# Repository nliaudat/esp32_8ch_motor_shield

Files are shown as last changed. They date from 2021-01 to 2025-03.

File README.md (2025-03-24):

# An ESP32 8 channels motor controller (shield) | Floor heating controller for proportional actuator
(Can replace Homematic IP Floor Heating Actuator [HmIP-FALMOT-C12] ~210$ + [CCU3] ~150$)



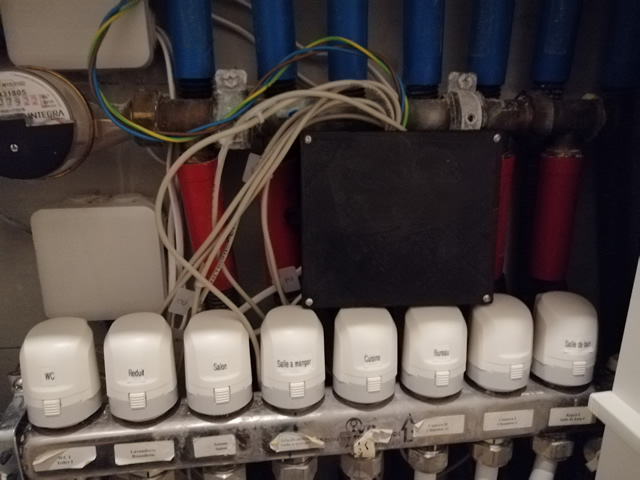
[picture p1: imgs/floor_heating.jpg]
floor_heating


The ready to go board costs less than 15$ (excluding shipping)

## Project rules : 
This project have rules : open hardware and sources, but not open-bar :)
* https://github.com/nliaudat/esp32_8ch_motor_shield/wiki/Project-rules

## 2 Goals : 

* Make a floor heating controller for proportionnal valves ([look at advantages of proportionnal valves](https://github.com/nliaudat/esp32_8ch_motor_shield/wiki/Advantages-of-proportionnal-valves-instead-of-on-off-valves) )
* ESP motor shield (done in v58 rev 1.49 )
    
## Functionalities : 
* Can control 8 DC motors or 4 steppers motor
* Can drive 8 Homematic valve actuators [HmIP-VDMOT] (~15$ each)
* The card use a ESP32-WROOM-32D as logics and wifi connection. (You can get a 32U if you want an external antenna).
* It now supports the ESP32-C3 supermini
* The software runs under esphome to be easy to customize and linked with https://www.home-assistant.io 
* Can be extended up to 16 channels (I recommend to get 2 boards for better performances, but the shifts registers can be extended up to 4 [shiftregOut](https://github.com/nliaudat/esp32_8ch_motor_shield/blob/main/shiftregOut.md))
* Use BEMF (back electromotive force) from motors to get endstops
* Can be directly linked to external temperature sensors (wifi,BLE, or via available [free pins](https://github.com/nliaudat/esp32_8ch_motor_shield/blob/main/extension.md))
* 2 onewire connectors (to have precise IN/OUT temperature control over heating circuit)
* USB-C power input or 5-12V input
* Easily [hackable](https://github.com/nliaudat/esp32_8ch_motor_shield/blob/main/hack.md)

## Fabrication : 

* PCB can be ordered with chips assembled at JLPCB for 13$/unit. (:warning: For old AC version, you have to isolate the AC part with tape)
* The new version use DC input only with usb-c up to 3A (or custom 5-12V input)
* ESP32-WROOM-32D devkit with 38 pin costs approx 3.8$ . The ESP32-C3 supermini approx 2.5$
* Box is 3D printed

## Firmware : 
* Floor heating : https://github.com/nliaudat/floor-heating-controller
* Motor control : https://github.com/nliaudat/esphome-8-ch-motor-controller

## The futur is : Diy proportionnal valves | smart proportional actuator (TRV) with Esp-C3 mcu
https://github.com/nliaudat/floor-heating-proportional-valve | need help !

## Produce your PCB Controller and Enclosure

We tried to ease the steps to get you going to produce the Enclosure and order/assemble your Controller-Board. Please have a look at 
the [`HOWTO get going`](./HOWTO_get_going_as_floor_heating_controller.md) documentation.

## PCB sharing
[https://oshwlab.com/nliaudat/floor_heatin_controller_v61](https://pro.easyeda.com/editor#id=15bc77acaa4147fca2a36e92e8cc8681)

## Licence: 
* Creative Commons Attribution-NonCommercial-ShareAlike 4.0 International (CC-BY-NC-SA)
* No commercial use

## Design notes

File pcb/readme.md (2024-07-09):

# Design printouts

All schematics and pcb are in https://github.com/nliaudat/esp32_8ch_motor_shield/releases

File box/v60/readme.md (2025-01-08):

Many thank @MrAges

https://github.com/nliaudat/esp32_8ch_motor_shield/discussions/70#discussioncomment-11770972

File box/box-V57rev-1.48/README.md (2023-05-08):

# Enclosure for version V57 rev 1.48
This enclosure is divided into two parts: the bottom and the top.

## Bottom enclosure
The bottom enclosure, named "bottomCase3dModel", is designed to accommodate a PCB and has 3 mounting holes (M3x8mm) to secure the PCB. Additionally, it has 4 holes to attach the enclosure to a wall. On the right side, there is an opening for a PG 9 4-8mm cable gland (PGS9) used for power cable mounting. At the front of the enclosure, there are 8 holes for RJ11 jacks.

## Top enclosure
The top enclosure comes in two versions:

"topCase3dModelwithWagoAndAntenna" includes additional WAGO holders and an opening for an SMA antenna jack. WAGO connectors are used to connect DS18B20 thermometers.

"topCase3dModel" is a plain version with no additional holes or mounting options.

The enclosure is 40mm high (52mm for the version with WAGO holders), 100mm wide, and 155mm long.

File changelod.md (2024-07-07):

## New version 1.3 : 
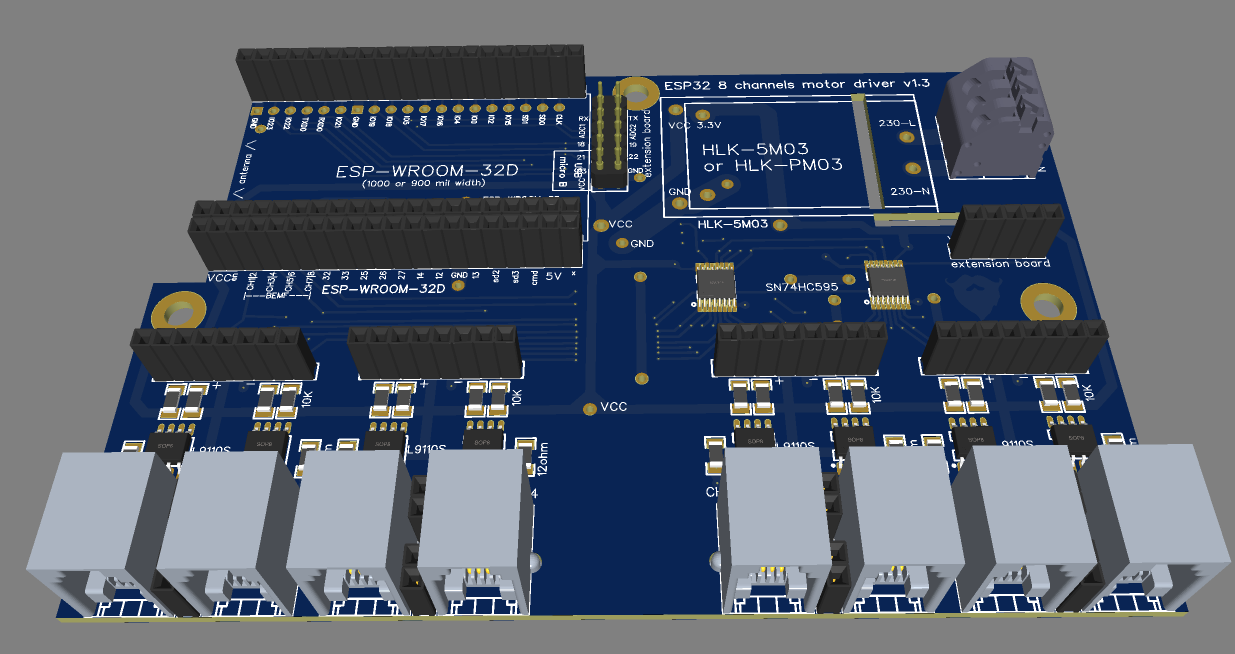
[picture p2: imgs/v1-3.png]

* Compatible with HKL-5M03 or HKL-PM03, or with 5V version (HKL-5M05 or HKL-PM05)
* Compatible with 1000 or 900 mil ESP32 board width

## New version 1.4 : 
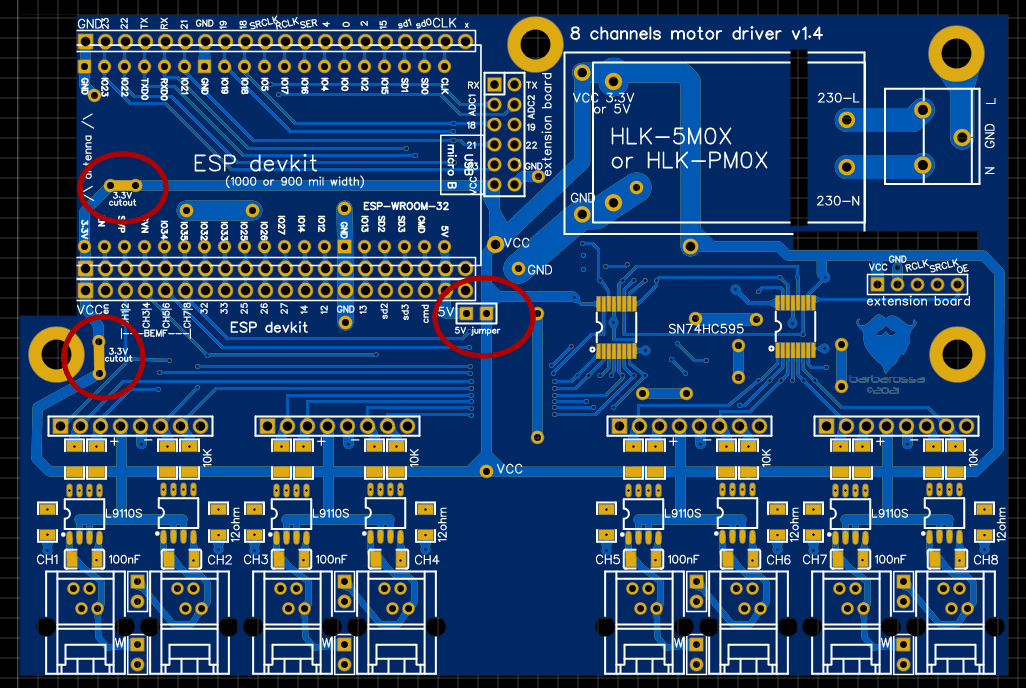
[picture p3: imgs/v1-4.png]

* Input power can be 5V to 12V
* 5V Jumper + 3.3V exposed copper cutout

## New version v53 rev 1.19 : 
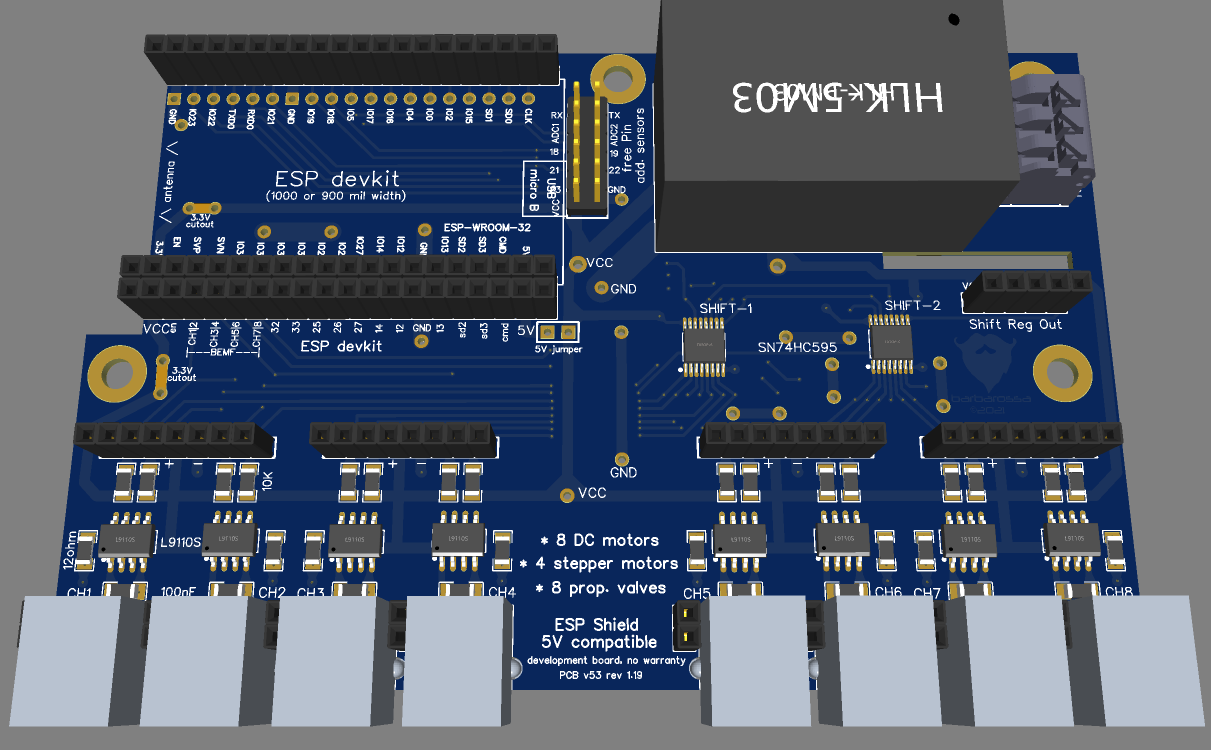
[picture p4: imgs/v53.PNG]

* Complete rebuild
* All part can be assembled at JLPCB
* Costs rise to 25$ / board (ESP not included, shipping included)
* Fix issue [#5] (https://github.com/nliaudat/esp32_8ch_motor_shield/issues/5)
* Fix HLK-PM03 footprint
* Change L9110s chips (the old one was not available anymore)
* change version number to real job

## New version v54 rev 1.34 : 
* Change 230V input socket with screw
* Fix regression in HLK-PM03 footprint
* Change resistors to 1.07 ohm

## New version with DC input power (4.9-18 V 5A - usb and DC 2.5/6.3 plug): 


## New version v54 rev 1.39 : 
* fix CH6 input shorted to CH7/8 BEMF [#27](https://github.com/nliaudat/esp32_8ch_motor_shield/issues/27)

## New version v55 rev 1.45 : 
* Add operational amplifier to ADC inputs

* Easyeda project getting [public](https://easyeda.com/editor#id=240c2bd91cde438f93348d56e1ae4e72|420e6f6085d643fc9c5df7bfbe9595bf|f15c181c211e4aebaf86420464abe718|b3e9b48180db4901b45d0292a792846e|60a1b0936f664eb8b9e5f7402068a21b|7744c3e75c54448eb9fed788f130dd96|78ed6c97623e4c1f929c753245e2f96b)

## New version v57 rev 1.48 : 
* Replace the 1.07R with 2 ohms
* Custom resistors for BEMF (exposed layer to cut out)
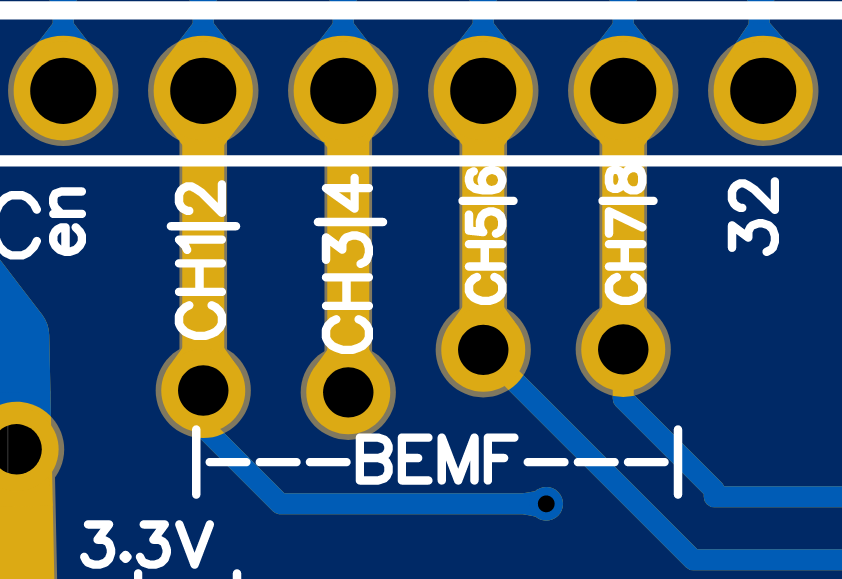
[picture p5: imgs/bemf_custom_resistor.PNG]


## New version v58 rev 1.49 : 
* Replace the RJ11 with screw terminals ( the RJ11 was too specific for "HmIP-VDMOT") (look at [VdMot wiring](https://github.com/nliaudat/esp32_8ch_motor_shield/blob/main/VDMOT_wiring.md))
* Make the board compatible with all kind of motors (2.5 to 6V)
* The easyeda sources are not available anymore (more than 50 developpers has anounced and nobody make a public commit since 3 years)
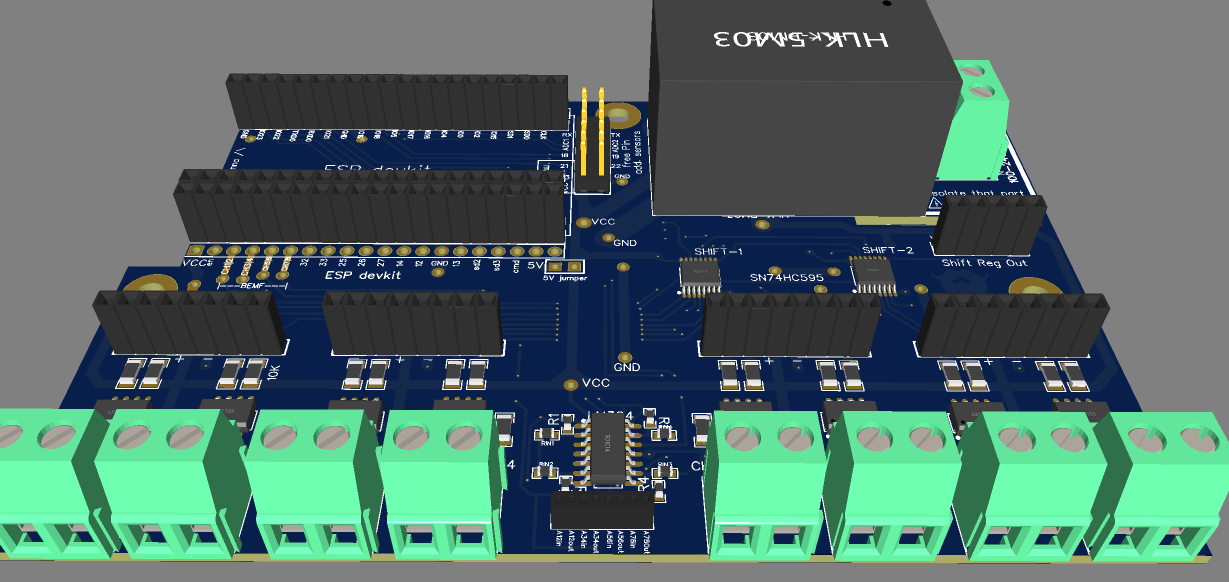
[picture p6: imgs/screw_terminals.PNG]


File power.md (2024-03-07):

# The shield itself:
* accept a wide supply voltage range from 3.3V to 12V
* 800mA continuous current output capability per channel
* peak current capability up to 2.0A

# AC Power for ESP : 
3.3v power can be HKL-5M03 or HKL-PM03 or anything else

# DC Power : 
Any DC-DC Buck Converter Step Down Module

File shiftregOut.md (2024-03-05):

To link a 2nd board (without esp32) , you can use the shift reg out pins : 



linked to the other pcb (without esp32)



QH' output must be linked to SER input

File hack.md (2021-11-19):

# Hackable
* Every board Pin has its own second weldable slot
* Can work with 5V controller board like Arduino series

## Samples :
#### Replacing BEMF resistors
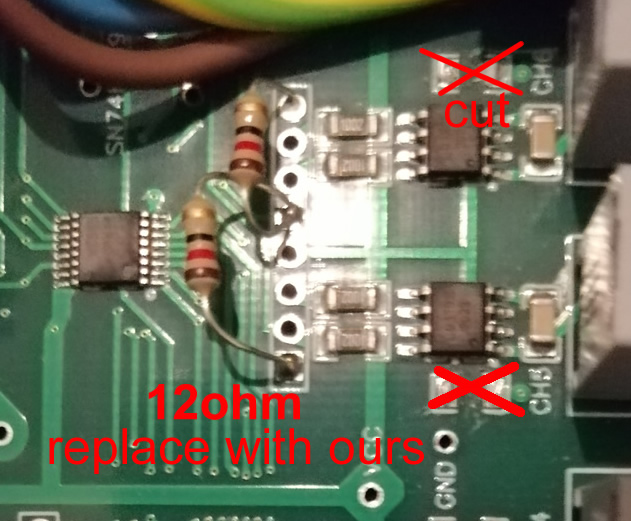
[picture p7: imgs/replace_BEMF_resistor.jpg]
replace BEMF resistor


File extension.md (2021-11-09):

They are 7 free pin available to add custom sensors

Capture

Capture2

Look at [schematics.pdf](https://github.com/nliaudat/esp32_8ch_motor_shield/blob/main/PCB/Schematic.pdf) for details.

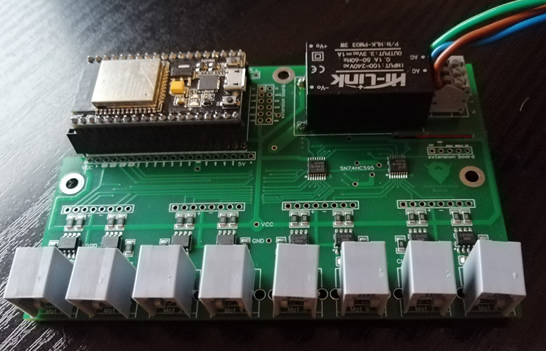
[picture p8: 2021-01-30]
imgs/board.jpg

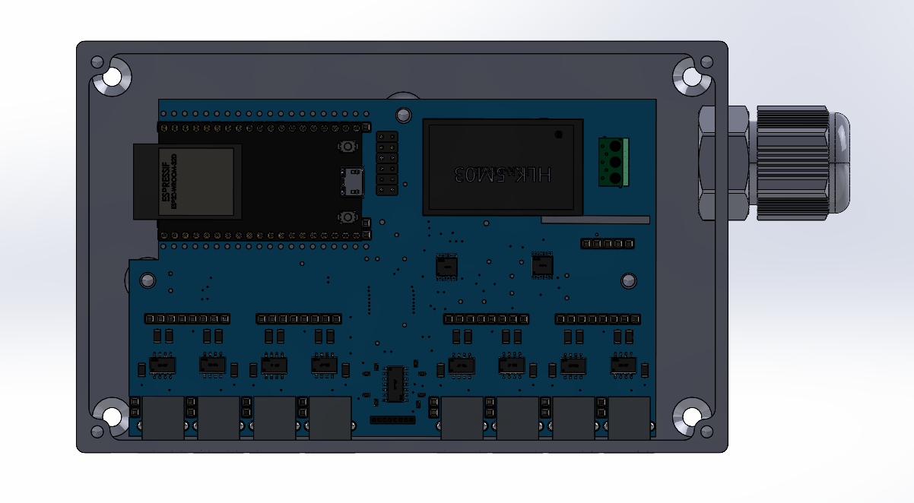
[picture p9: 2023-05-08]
box/box-V57rev-1.48/img/bottomCase3dModel - model2.png

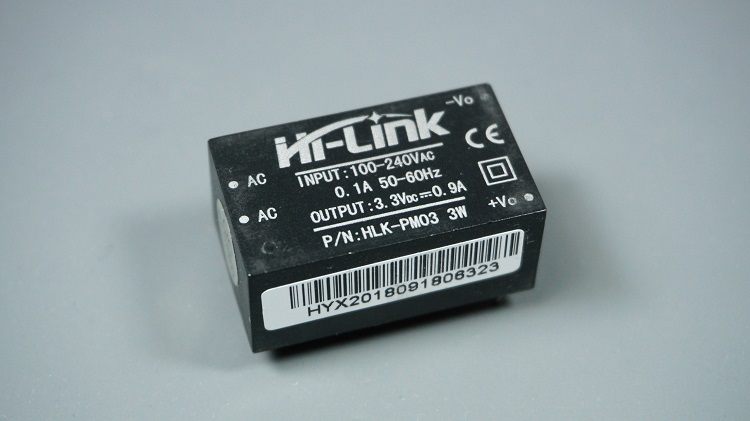
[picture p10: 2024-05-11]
imgs/HLK-PM03.jpg

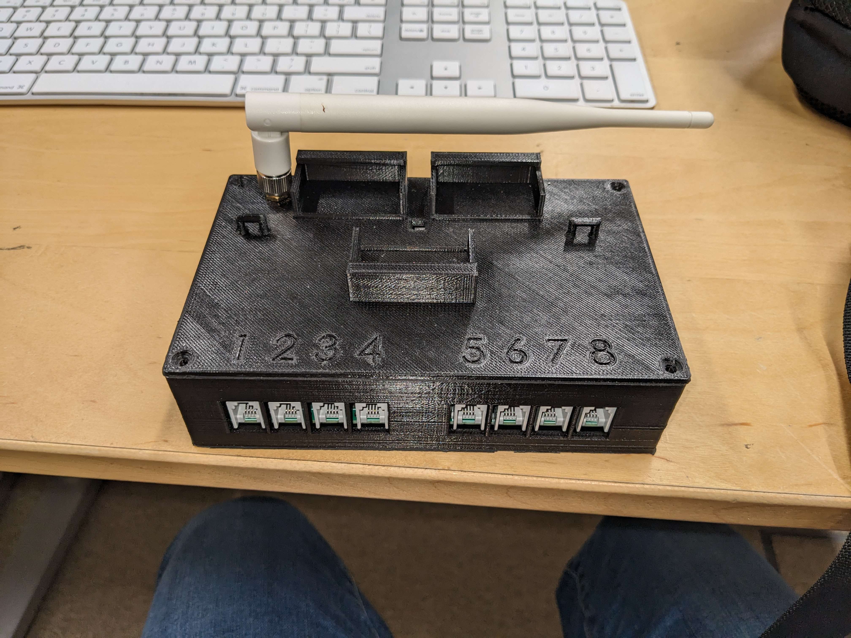
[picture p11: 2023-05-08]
box/box-V57rev-1.48/img/topCase3dModelwithWagoAndAntenna - real photo 2.jpg

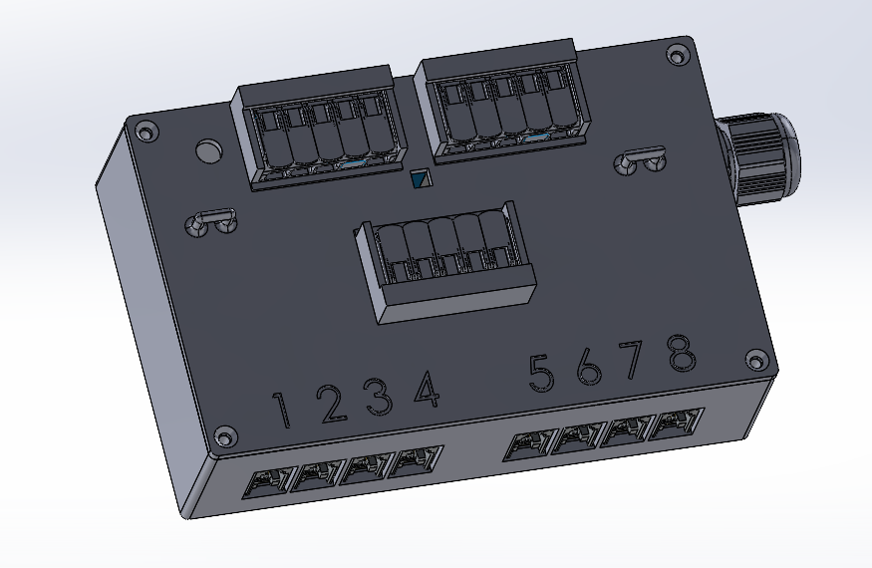
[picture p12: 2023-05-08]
box/box-V57rev-1.48/img/topCase3dModelwithWagoAndAntenna - model.png

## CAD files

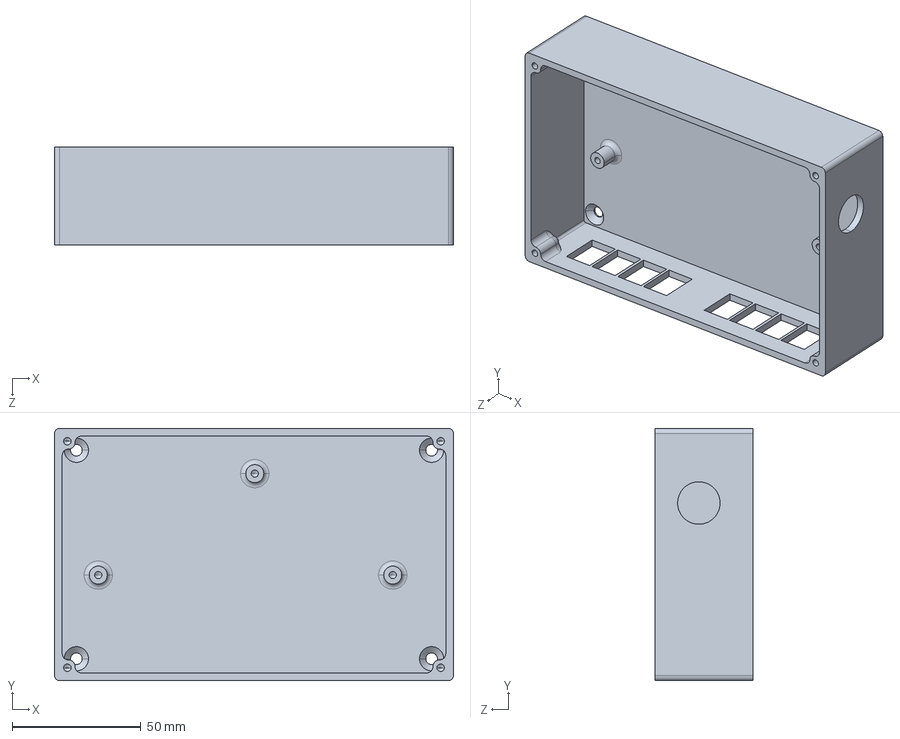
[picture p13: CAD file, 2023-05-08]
box/box-V57rev-1.48/bottomCase3dModel.STEP
155.0 x 98.0 x 38.0 mm

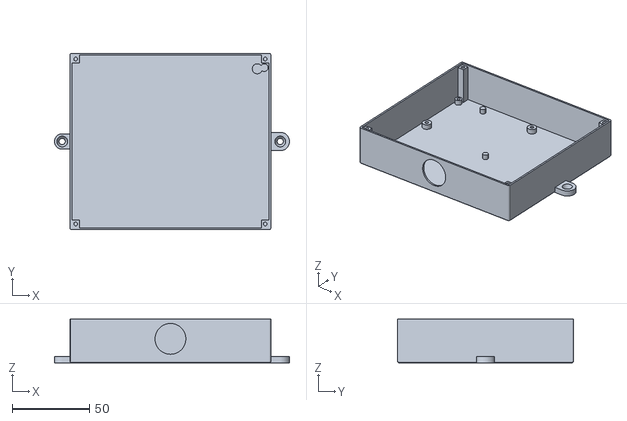
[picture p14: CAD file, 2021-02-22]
box/general/PCB_box_generator_body.stl
152.5 x 114.5 x 28.4

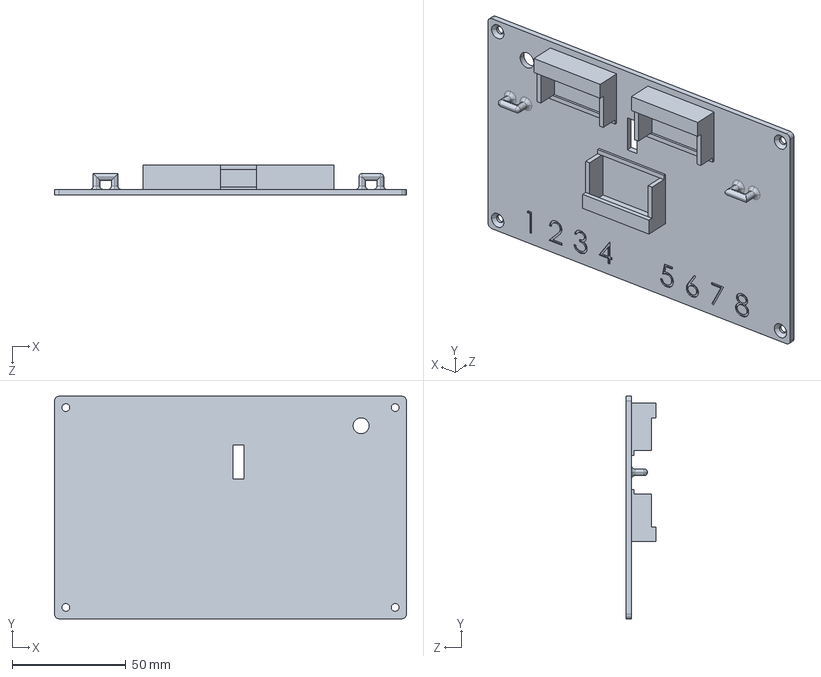
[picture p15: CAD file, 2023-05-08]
box/box-V57rev-1.48/topCase3dModelwithWagoAndAntenna.STEP
155.0 x 98.0 x 13.3 mm

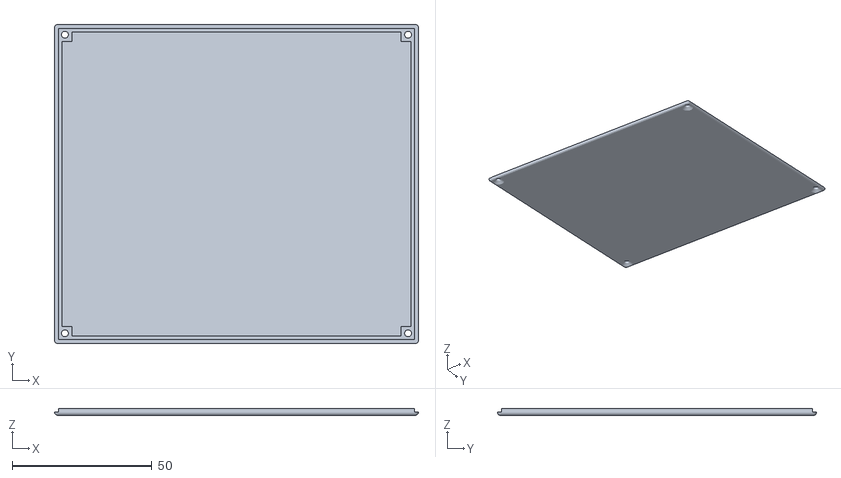
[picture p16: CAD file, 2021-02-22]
box/general/PCB_box_generator_cover.stl
130.5 x 114.5 x 2.48

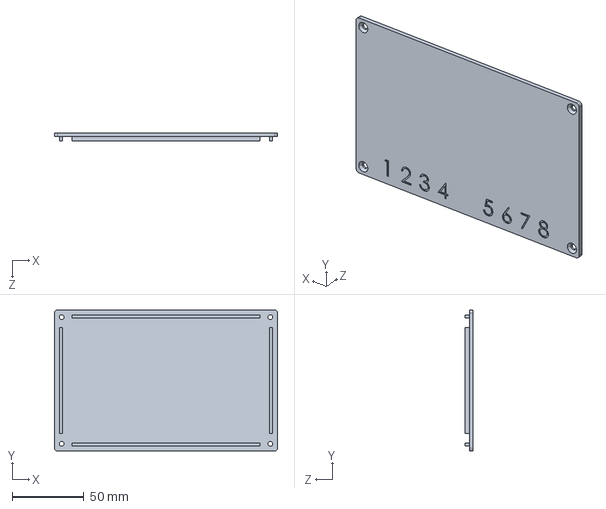
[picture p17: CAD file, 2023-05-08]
box/box-V57rev-1.48/topCase3dModel.STEP
155.0 x 98.0 x 5.50 mm

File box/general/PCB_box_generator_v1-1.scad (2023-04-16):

/* [Description] */
//preset description (any text):
preset_descr = "";
//preset version:
preset_ver = "1.0";

/* [Render] */
//minium angle (degrees):
$fa = 1.01;
//minium size (mm):
$fs = 0.41;
//prepare model for 3D-printing:
printing_mode = 1; // [1:True, 0:False]
//show box cover:
show_cover = 1; // [1:True, 0:False]
//show box body:
show_body = 1; // [1:True, 0:False]
//show PCB bounding box:
show_pcb = 1; // [1:True, 0:False]
//box cover distance (mm):
box_cover_dist = 10; // [0:2:20]
//box cover transparency:
box_cover_a = 0.85; // [0.65:0.05:1]

/* [Hidden] */
overlap = 0.005; //overlap value

HT_SQUARE = 1;  //hole types enum
HT_CIRCLE = 2;

HP_NONE = 0; //hole & txt sides enum
HP_COVER = 1;
HP_BOTTOM = 2;
HP_FORWARD = 3;
HP_BACKWARD = 4;
HP_LEFT = 5;
HP_RIGHT = 6;

//=> box = 60x45x30
/* [PCB] */
//PCB size x (mm):
pcb_size_x = 60.1;
//PCB size y (mm):
pcb_size_y = 45.1;
//PCB max height from top PCB side (mm):
pcb_top_height = 30.1;
//PCB board thickness (mm):
pcb_thickness = 1.6; // [0.5:0.1:30]
//PCB max height from bottom PCB side (mm):
pcb_bottom_height = 0.1;
//PCB hole offset from the border along x (mm):
pcb_hole_offset_x = 2.1;
//PCB hole offset from the border along y (mm):
pcb_hole_offset_y = 2.1;
//PCB hole diameter (mm):
pcb_hole_diameter = 2.1; // [1:0.1:10]
//screw rod length (mm):
pcb_screw_length = 5; // [0:0.1:20]
//generate PCB sleeves:
pcb_sleeve = 1; // [1:True, 0:False]

/* [Box] */
//box inner margin (mm):
inner_margin = 1; // [0:0.25:10]
//box wall thickness (mm):
wall_thickness = 1.25; // [1:0.05:10]
//box screw hole diameter (mm):
hole_diameter = 3; // [1:0.1:5]
//box screw length (mm):
screw_length = 10; // [1:0.1:20]
//box cover screw chamfer (mm):
hole_chamfer = 6.5; // [1:0.5:10]
//gap between box cover and body (mm):
print_tolerance = 0.25; // [-0.25:0.05:1]

/* [Holes] */
//Hole: [type, side, pos_x, pos_y, width/diameter, height, skirt_width, skirt_height+, skirt_height-]; type: (0=none, 1=suare, 2=circle); side: (1=cover, 2=bottom, 3=forward, 4=backward, 5=left, 6=right)
h1v = [0, 0, 0, 0, 0, 0, 0, 0, 0];
h2v = [0, 0, 0, 0, 0, 0, 0, 0, 0];
h3v = [0, 0, 0, 0, 0, 0, 0, 0, 0];
h4v = [0, 0, 0, 0, 0, 0, 0, 0, 0];
h5v = [0, 0, 0, 0, 0, 0, 0, 0, 0];
h6v = [0, 0, 0, 0, 0, 0, 0, 0, 0];
h7v = [0, 0, 0, 0, 0, 0, 0, 0, 0];
h8v = [0, 0, 0, 0, 0, 0, 0, 0, 0];
h9v = [0, 0, 0, 0, 0, 0, 0, 0, 0];
h10v = [0, 0, 0, 0, 0, 0, 0, 0, 0];
h11v = [0, 0, 0, 0, 0, 0, 0, 0, 0];
h12v = [0, 0, 0, 0, 0, 0, 0, 0, 0];
h13v = [0, 0, 0, 0, 0, 0, 0, 0, 0];
h14v = [0, 0, 0, 0, 0, 0, 0, 0, 0];
h15v = [0, 0, 0, 0, 0, 0, 0, 0, 0];
h16v = [0, 0, 0, 0, 0, 0, 0, 0, 0];
h17v = [0, 0, 0, 0, 0, 0, 0, 0, 0];
h18v = [0, 0, 0, 0, 0, 0, 0, 0, 0];
h19v = [0, 0, 0, 0, 0, 0, 0, 0, 0];
h20v = [0, 0, 0, 0, 0, 0, 0, 0, 0];
h21v = [0, 0, 0, 0, 0, 0, 0, 0, 0];
h22v = [0, 0, 0, 0, 0, 0, 0, 0, 0];
h23v = [0, 0, 0, 0, 0, 0, 0, 0, 0];
h24v = [0, 0, 0, 0, 0, 0, 0, 0, 0];
h25v = [0, 0, 0, 0, 0, 0, 0, 0, 0];
h26v = [0, 0, 0, 0, 0, 0, 0, 0, 0];
h27v = [0, 0, 0, 0, 0, 0, 0, 0, 0];
h28v = [0, 0, 0, 0, 0, 0, 0, 0, 0];
h29v = [0, 0, 0, 0, 0, 0, 0, 0, 0];
h30v = [0, 0, 0, 0, 0, 0, 0, 0, 0];
h31v = [0, 0, 0, 0, 0, 0, 0, 0, 0];
h32v = [0, 0, 0, 0, 0, 0, 0, 0, 0];

/* [Sleeves] */
//Sleeve: [side, pos_x, pos_y, diameter, skirt_width, skirt_height+, height-]; side: (0=none, 1=cover, 2=bottom, 3=forward, 4=backward, 5=left, 6=right)
s1v = [0, 0, 0, 0, 0, 0, 0];
s2v = [0, 0, 0, 0, 0, 0, 0];
s3v = [0, 0, 0, 0, 0, 0, 0];
s4v = [0, 0, 0, 0, 0, 0, 0];
s5v = [0, 0, 0, 0, 0, 0, 0];
s6v = [0, 0, 0, 0, 0, 0, 0];
s7v = [0, 0, 0, 0, 0, 0, 0];
s8v = [0, 0, 0, 0, 0, 0, 0];
s9v = [0, 0, 0, 0, 0, 0, 0];
s10v = [0, 0, 0, 0, 0, 0, 0];
s11v = [0, 0, 0, 0, 0, 0, 0];
s12v = [0, 0, 0, 0, 0, 0, 0];

/* [Mounts] */
//Mount: [side, shift, width, height, hole_diameter, hole_chamfer]; side: (1=forward, 2=right, 3=backward, 4=left)
m1v = [0, 0, 0, 0, 0, 0];
m2v = [0, 0, 0, 0, 0, 0];
m3v = [0, 0, 0, 0, 0, 0];
m4v = [0, 0, 0, 0, 0, 0];
m5v = [0, 0, 0, 0, 0, 0];
m6v = [0, 0, 0, 0, 0, 0];
m7v = [0, 0, 0, 0, 0, 0];
m8v = [0, 0, 0, 0, 0, 0];
m9v = [0, 0, 0, 0, 0, 0];
m10v = [0, 0, 0, 0, 0, 0];
  
/* [Hole array] */
//Hole array: [type, side, pos0_x, pos0_y, width/diameter, height, count_x, count_y, step_x, step_y]; type: (0=none, 1=suare, 2=circle); side: (1=cover, 2=bottom, 3=forward, 4=backward, 5=left, 6=right)
ha1v = [0, 0, 0, 0, 0, 0, 0, 0, 0, 0];
ha2v = [0, 0, 0, 0, 0, 0, 0, 0, 0, 0];
ha3v = [0, 0, 0, 0, 0, 0, 0, 0, 0, 0];
ha4v = [0, 0, 0, 0, 0, 0, 0, 0, 0, 0];
ha5v = [0, 0, 0, 0, 0, 0, 0, 0, 0, 0];
ha6v = [0, 0, 0, 0, 0, 0, 0, 0, 0, 0];
ha7v = [0, 0, 0, 0, 0, 0, 0, 0, 0, 0];
ha8v = [0, 0, 0, 0, 0, 0, 0, 0, 0, 0];

/* [Text] */
//Text: [side, str, pos_x, pos_y, size, height]; side: (0=none, 3=forward, 4=backward, 5=left, 6=right)
t1v = [0, "", 0, 0, 0, 0];
t2v = [0, "", 0, 0, 0, 0];
t3v = [0, "", 0, 0, 0, 0];
t4v = [0, "", 0, 0, 0, 0];
t5v = [0, "", 0, 0, 0, 0];
t6v = [0, "", 0, 0, 0, 0];
t7v = [0, "", 0, 0, 0, 0];
t8v = [0, "", 0, 0, 0, 0];
t9v = [0, "", 0, 0, 0, 0];
t10v = [0, "", 0, 0, 0, 0];

//box sleeve thickness and height
sleeve_tk = wall_thickness * 1; //sleeve thickness ratio
sleeve_th = pcb_bottom_height > (pcb_screw_length - pcb_thickness) ? pcb_bottom_height : pcb_screw_length - pcb_thickness + 0.25;
sleeve_bh = pcb_sleeve == 0 ? 0 : sleeve_th;

//pcb bottom part height
pcb_bph = pcb_sleeve == 1 ? sleeve_bh : pcb_bottom_height;

//box inner size x, y, z
box_sx = pcb_size_x + inner_margin * 2;
box_sy = pcb_size_y + inner_margin * 2 + 2 * hole_diameter + 4 * sleeve_tk;
box_sz = inner_margin + pcb_top_height + pcb_thickness + pcb_bph;

//half of x, y, z
box_hsx = box_sx / 2;
box_hsy = box_sy / 2;
box_hsz = box_sz / 2;

//default z pos for holes, sleeves, etc
default_z = wall_thickness + pcb_bph + pcb_thickness / 2; //is center of pcb


//make body if enabled (makerbot customizer dont show checkboxes?)
if (show_body == 1)
  BoxBody();
    
//make cover if enabled
if (show_cover == 1) {
  //move cover if printing mode enabled
  cover_rot = printing_mode == 1 ? 180 : 0;
  cover_mov = printing_mode == 1 ? 2*box_hsx + 2*wall_thickness + 10 + 2*box_cover_dist : 0;
  cover_flg = printing_mode == 1 ? 1 : 0;
  
  translate([0, 0, cover_flg*(box_sz + 2 * wall_thickness + box_cover_dist + overlap)])
    rotate([cover_rot, 0, 0])
      translate([cover_mov, 0, 0])
        BoxCover();
}


//show pcb bounding box if enabled
if ((show_pcb == 1) && (printing_mode != 1)) {
  translate([-pcb_size_x/2, -pcb_size_y/2, wall_thickness + pcb_bph]) {
    color([0.5,1,0.5], alpha=0.6) //pcb bottom height - green
      translate([0, 0, -pcb_bottom_height+overlap])
        cube([pcb_size_x, pcb_size_y, pcb_bottom_height]);
    color([1,0.5,0.5], alpha=0.5) //pcb top height - red
      translate([0, 0, pcb_thickness])
        cube([pcb_size_x, pcb_size_y, box_sz - inner_margin - pcb_bph - pcb_thickness]);
          color([0.5,0.5,1], alpha=0.55) //pcb thickness - blue
    cube([pcb_size_x, pcb_size_y, pcb_thickness - overlap]);
  }
}

//generate 1 from 4 chamfers for cover
//input: inv_x, inv_y - for box corner num definition
module ChamferCover(inv_x, inv_y) {
  translate([inv_x * box_hsx + inv_x * overlap + (-inv_x) * hole_diameter / 2 + sleeve_tk * (-inv_x), inv_y * box_hsy + inv_y * overlap + (-inv_y) * hole_diameter / 2 + sleeve_tk * (-inv_y), (-overlap)]) {
          cylinder(d2 = hole_diameter, d1 = hole_chamfer, h = wall_thickness + 3 * overlap);
          cylinder(d=hole_diameter, h = 10 * wall_thickness, center=true); 
  }
}


//generate 1 from 4 sleeves for pcb on box body
//input: inv_x, inv_y - for box corner num definition
module SleevePCB(inv_x, inv_y){
    translate([inv_x * pcb_size_x / 2 + (-inv_x) * pcb_hole_offset_x, inv_y * pcb_size_y / 2 + (-inv_y) * pcb_hole_offset_y, wall_thickness - overlap])
    difference() {
        cylinder(d = pcb_hole_diameter + 2 * sleeve_tk, h = sleeve_bh);
        translate([0, 0, (-overlap)]) cylinder(d = pcb_hole_diameter, h = sleeve_bh + 2 * overlap);
    }
}


//generate 1 from 4 sleeves on box body for cover
//input: inv_x, inv_y - for box corner num definition
module SleeveBody(inv_x, inv_y, rot_z){
    translate([inv_x * box_hsx + inv_x * overlap, inv_y * box_hsy + inv_y * overlap, wall_thickness - overlap]) {
      difference() {
        rotate([0, 0, rot_z])
          cube([hole_diameter + 2 * sleeve_tk, hole_diameter + 2 * sleeve_tk, box_sz - wall_thickness]);
        translate([(-inv_x) * hole_diameter / 2 + 2 * overlap * (-inv_x) + sleeve_tk * (-inv_x), (-inv_y) * hole_diameter / 2 + 2 * overlap * (-inv_y) + sleeve_tk * (-inv_y), box_sz - screw_length - wall_thickness + overlap])
          cylinder(d=hole_diameter, h=screw_length);
      }
    }
}
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

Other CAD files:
box/box-V57rev-1.48/topCase3dModel.STL

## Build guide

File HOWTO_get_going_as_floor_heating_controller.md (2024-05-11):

# Fabrication of your PCB Controller and Enclosure

Before you are purchasing a given release of `esp32_8ch_moter_shield` controller
board, please have a look inside the [`Images`](./imgs) folder. You
should prefere to order the latest stable release-version. To allow
generic cabeling to valve actuators, the controller board did exchange
the former RJ11 plugs in favor of screw terminals since
[version 58](./imgs/v58_rev_1.49.jpg).

It is possible to link multiple boards via the [**shift reg out pins**](./shiftregOut.md).
The ready to go board can be produced for less than 30$.



## Enclosures / Controller Cases

Have a look at the [`Boxing`](./box) directory. Yo uwill find 3D
printable models (STL files), to print out a working cases for supported
`esp32_8ch_moter_shield` controllers.

Just to give you an idea, the following pictures show the top and bottom cases suitable for version 57


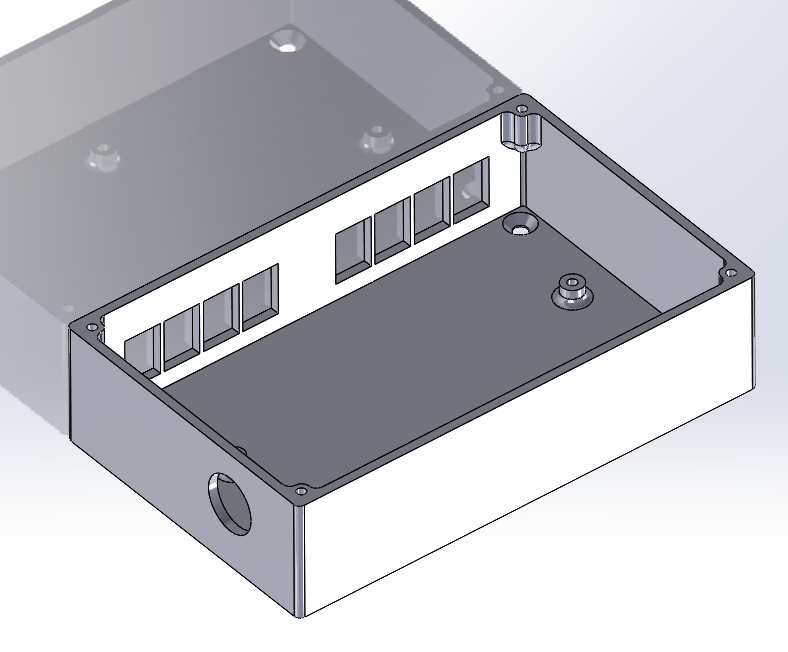
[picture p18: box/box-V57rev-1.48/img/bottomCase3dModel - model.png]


If you are unfamiliar with the 3D Printing, have a look at
[3D Printing Overview](https://3dprinting.com/what-is-3d-printing)
to get an idea on how it works. You may use your own 3D printer or make
use of a commercial service.

## Supported valves

You may choose from the list of following supported valves to contol your floor heating cirquits:

- [`DIY proportional valves`](https://github.com/nliaudat/floor-heating-proportional-valve):
  This is a standalone valve which do not need a controller. You can run it without the ESP-C3 board, but the distance sensor will not work.
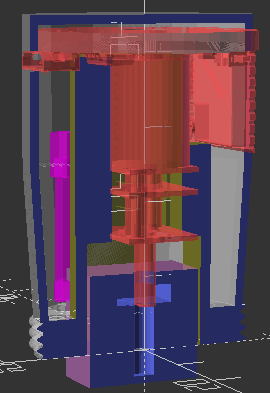
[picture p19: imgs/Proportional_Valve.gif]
  
  - Pricing: aprox 8.8$ each

- All DC valve from range 3V3 to 12V should work.
  You only need to change the power supply according to your valve
  Link the >5v jumper and cut the 3V3 cutout as in https://github.com/nliaudat/esp32_8ch_motor_shield/raw/main/imgs/v1-4.png

  As example, the "Equiva Model N" is a 3v3 valve that works

-  Floor Heating Actuator:
  [`HmIP-VDMOT`](https://de.elv.com/homematic-ip-stellantrieb-motorisch-fuer-fussbodenheizung-hmip-vdmot-153309).
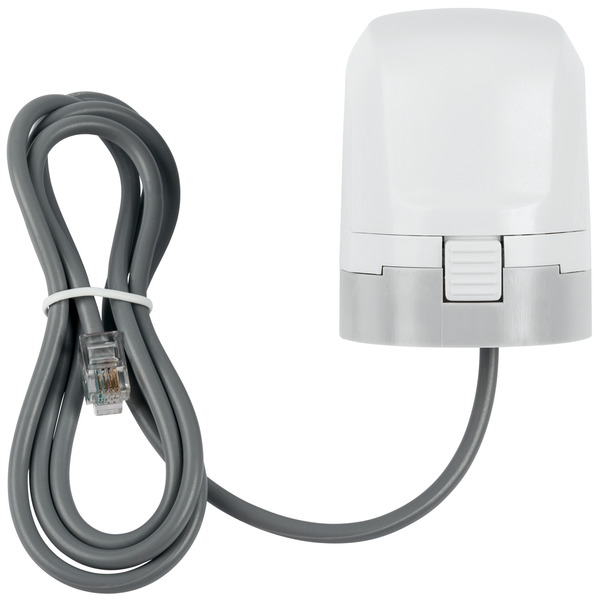
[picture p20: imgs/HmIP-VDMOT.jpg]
  
  - Pricing: approx 15$ each
  - Please consult [VDMOT-Wirering](./VDMOT_wiring.md) document, that explains
    how to cut and connect the RJ11 equipted cables.

## Order via JLPCB

Before you can place an order, you have to register or login to your
JLPCB account. Please consult the official JLPCB order guide:
[How to place an Order](https://jlcpcb.com/help/article/54-How-do-I-place-an-order).

* The PCB can be ordered **with chips assembled** at JLPCB
  Pricing: approx 5.8$/unit.
  (**Warning**: You have to isolate the AC part with tape)

* The 3.3v power (or 5v) can be HKL-5MX or HKL-PMX
  Pricing: approx 2.75$
* ESP32-WROOM-32D
  Pricing: approx 3.8$

## Power Adapters

### Shield

* accept a wide supply voltage range from 3.3V to 12V
* 800mA continuous current output capability per channel
* peak current capability up to 2.0A

### AC Power

The Controller itself will need an 3.3 Volt AC Power input.

To power the onboard ESP assemble the board from any of the
following step-down power supply modules:

- Hi-Link [HKL-5M03](./imgs/HLK-5M03.jpg): Input 100-240VAC/50-60Hz; Output 3.3VDC/5W
- Hi-Link 3W [HKL-PM03](./imgs/hlk-pm03.jpg): Input 100-240VAC/0.1A/50-560Hz; Output 3.3VDC/0.9A/5W
- anything else suitable

### DC Power
You can supply any DC-DC buck converter step down module.

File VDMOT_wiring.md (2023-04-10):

# The latest screw terminal board need to cut the VdMot cable

Only the Green and White cable are needed. 
The Green goes to the right of the screw terminal to keep compatibility with the old RJ11 terminal

vdmot

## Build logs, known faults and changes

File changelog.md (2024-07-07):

## New version 1.3 : 

* Compatible with HKL-5M03 or HKL-PM03, or with 5V version (HKL-5M05 or HKL-PM05)
* Compatible with 1000 or 900 mil ESP32 board width

## New version 1.4 : 

* Input power can be 5V to 12V
* 5V Jumper + 3.3V exposed copper cutout

## New version v53 rev 1.19 : 

* Complete rebuild
* All part can be assembled at JLPCB
* Costs rise to 25$ / board (ESP not included, shipping included)
* Fix issue [#5] (https://github.com/nliaudat/esp32_8ch_motor_shield/issues/5)
* Fix HLK-PM03 footprint
* Change L9110s chips (the old one was not available anymore)
* change version number to real job

## New version v54 rev 1.34 : 
* Change 230V input socket with screw
* Fix regression in HLK-PM03 footprint
* Change resistors to 1.07 ohm

## New version with DC input power (4.9-18 V 5A - usb and DC 2.5/6.3 plug): 


## New version v54 rev 1.39 : 
* fix CH6 input shorted to CH7/8 BEMF [#27](https://github.com/nliaudat/esp32_8ch_motor_shield/issues/27)

## New version v55 rev 1.45 : 
* Add operational amplifier to ADC inputs

* Easyeda project getting [public](https://easyeda.com/editor#id=240c2bd91cde438f93348d56e1ae4e72|420e6f6085d643fc9c5df7bfbe9595bf|f15c181c211e4aebaf86420464abe718|b3e9b48180db4901b45d0292a792846e|60a1b0936f664eb8b9e5f7402068a21b|7744c3e75c54448eb9fed788f130dd96|78ed6c97623e4c1f929c753245e2f96b)

## New version v57 rev 1.48 : 
* Replace the 1.07R with 2 ohms
* Custom resistors for BEMF (exposed layer to cut out)


## New version v58 rev 1.49 : 
* Replace the RJ11 with screw terminals ( the RJ11 was too specific for "HmIP-VDMOT") (look at [VdMot wiring](https://github.com/nliaudat/esp32_8ch_motor_shield/blob/main/VDMOT_wiring.md))
* Make the board compatible with all kind of motors (2.5 to 6V)
* The easyeda sources are not available anymore (more than 50 developpers has anounced and nobody make a public commit since 3 years)


## New version v59 rev 1.35 : 

**Better BEMF :** 

- Complete new concept of sensing with no more troubles with resistors to GND


**Remove of AC input :** 

- That was dangerous 
- The cost of HKL-5M was 3.8$ instead of 0.5$ for the new XL1509 module
- 

- With XL1509 module, You can adjust power of motors between 3.3V to 37V (recommended max 12V as not tested)
- Everybody has an old AC/DC 1A charger
- JLCPCB was charging a lot of shipping with the wheight of HKL module
- New DC power input : DC Power Receptacle 2mm 6.4mm + Screw terminal
- 


**Motor DC  :** 

- input can be 3.3V to 12V 
- a new AMS1117-3.3 powers the ESP32 board

**Better PCB :** 

- Separate 3.3V power of ESP32 board from motors
- Capacitor added to regulate peaks in power
- Via shielding
- Power isolation on bottom side
- Smaller design (126x70mm instead of 126x80). The M4 holes are compatible. 
- Lower the price of all components (jlcpcb price soldered)
- use R0402 footprint if possible 

**ESP32-C3  :** 

-  ESP32-C3 supermini footprint added 
-  ESP32-C3 costs 2.4$ instead of 3.8$ for nodemcu devkit

**OneWire :** 

- Add 3 onewire XH2.54-3P connectors
- Can get input temperature and output temperature of the heating circuit. 

**Studies :** 

- The XL9535 shift register cost the same as 2x SN74HC595, but the esphome code is very new and move to I2C is not compatible with esp-c3 supermini
- The Mini L298N module instead of L9110 soldered is approx the same price (0.7per channel out of 0.52 + resistors)
- Add more channels : if 12, this needs of another opam

**V59 :** 


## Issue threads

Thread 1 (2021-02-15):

Could you push your EDA Files

melad, 2021-02-15:
Hi,

first of all thank you for the greate work.
I would like to extend your board with onewire tempreature sensors. Could you push your EDA files ?

Thanks

nliaudat, 2021-02-16:
There are 2 extension board slots. You can wire anything from it.
Putting a temperature sensor on that board is a nonsens.

Closed 2021-02-16.

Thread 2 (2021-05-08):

Request for clarification

nbostrom, 2021-05-08:
<!-- READ THIS FIRST:
 - This is for feature requests only, for issues please go to the issues repository.
 - Please be as descriptive as possible, especially use-cases that can otherwise not be solved boost the problem's priority.

 DO NOT DELETE ANY TEXT from this template! Otherwise the issue may be closed without a comment.
-->

**Describe the problem you have/What new integration you would like**
<!-- A description of what you want to happen. -->
First of all, nice work! I have been looking for something like this since we bought our new house. Off the shelf products are unreasonable expensive. I'm a programmer, but I don't have much experience in electronics and embedded software, tho I do have some soldering experience. I'm sorry if I'm not supposed to use the issue board for these kind of questions, but I couldn't find any other contact information. So I guess you that you can see this feature request as a request for some clarification in the docs, if you like.

- Do you have any specific recommendations around the parameters when ordering assembled boards from JLPCB? I have never done anything similar before.
- I have 13 valves to control. In the readme you recommend getting two boards. Do you mean two completely separate boards with one ESP32 per board?

Thanks again. I hope that I can contribute with a DIN-compatible box with seperate holes for the contacts and maybe help iterate on the software part.

**Please describe your use case for this integration and alternatives you've tried:**
<!-- A clear and concise description of what the problem is. -->

**Additional context**
<!-- Add any other context about the feature request here. -->

<!-- LEAVE THIS LINE AS-IS AND DON'T DELETE IT, OTHERWISE THE FEATURE REQUEST WILL BE CLOSED AUTOMATICALLY. -->

nliaudat, 2021-05-08:
Hi,
For JLPCB, no special parameters, 2 layers are mandatory.

To control 13 valves, it depends on your programmation and valves : Esp32 has limited ACD sensor available if wifi enable (look at https://github.com/nliaudat/esp32_8ch_motor_shield/blob/main/PCB/Schematic.pdf)

Actually, 2 valves are on the same ADC sensor and do not run at the same time to have a precise BEMF (endstops). The pcb has 2 free ADC sensors available for a future extension board. In your case, I recommend 2 separate pcb with an Esp32 per board.

If you want to spare 4$ for the second ESP32, you can control the second board with the primary board. You'll have limited ADC sensors but it would work as expected.

I have that board in production for 1 year controlled by hassio, with homematic valves. That kink of valves are not very strong and I've made my own as replacement. The why I've made that pcb is I cannot control the main heating temperature (set for all appartments). The previous solution are on/off only and I wanted to have the solution to open the valve 10% only.

If you can set the main water temperature, that pcb is useless.

The future improvement will be a real webserver to set temperatures. With Esphome, the webserver is for debug purpose only. I haven't done it cause set the temperatures with hassio.

Regards.

nbostrom, 2021-05-08:
Hi,
Thanks for the clarifications. Much appreciated!

I can indeed control the main heating temperature heating curve, based on the outside temperature. But my problem is balancing, which becomes very cumbersome when you have 13 valves. Being able to partially open the valves is gold. I hope to be able to automatically balance the valves through software.

I do not think that the extra delay that comes with only running one actuator at a time will be a problem. Our heating tubes are  mold into the concrete and the heating delay is very large either way.

Do you mean that you created your own valve actuators? If so, that's very cool. What problems did you encounter with the homematic actuators? Did they break?

nliaudat, 2021-05-09:
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

some Homematic valve do not support the pressure and "unclip"

nbostrom, 2021-05-09:
I see. Thanks for the heads up!

Closed 2021-05-14.

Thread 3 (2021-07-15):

EasyEDA Project source

rubenmuehlhans, 2021-07-15:
Awesome work! Thank you!
I need to drive 10 Homematic valve actuators. Would you like to share your easyeda project source, so that i can update the pcb layout?

nliaudat, 2021-07-16:
I do not share the PCB source cause I'll will commercialize soon.
For 5.8$, you can got a second PCB card and use it as an extension board or a standalone (recommended)

nstadigs, 2021-07-19:
> I'll will commercialize soon

Great to hear! If the price is right I'll buy two of them :)

Closed 2021-07-16.

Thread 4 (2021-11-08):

[FEATURE REQUEST] add temp. sensor for VL and RL per channel for doing thermal balancing?

linuxdep, 2021-11-08:
<!-- READ THIS FIRST:
 - This is for feature requests only, for issues please go to the issues repository.
 - Please be as descriptive as possible, especially use-cases that can otherwise not be solved boost the problem's priority.

 DO NOT DELETE ANY TEXT from this template! Otherwise the issue may be closed without a comment.
-->

**Describe the problem you have/What new integration you would like**
<!-- A description of what you want to happen. -->
For thermal balancing i think it was nice to measure VL and RL and calculate thermal balancing automatically.
What do you think is this possible?
That would be the killer application, install underfloor heating, control it, thermal balancing is done automatically. Suspension of control for the valves marked as closed.

**Please describe your use case for this integration and alternatives you've tried:**
<!-- A clear and concise description of what the problem is. -->

**Additional context**
<!-- Add any other context about the feature request here. -->

<!-- LEAVE THIS LINE AS-IS AND DON'T DELETE IT, OTHERWISE THE FEATURE REQUEST WILL BE CLOSED AUTOMATICALLY. -->

nliaudat, 2021-11-08:
Please give a definition of your mean of VL and RL (German abbreviation ?)
At best a calculation formula.

Actually, the target position of valve is calculated with a simplification of arduino map function :
```
arduino map function :  return (x - in_min) * (out_max - out_min) / (in_max - in_min) + out_min;
with parameters : in_min=-1;in_max=1;out_min=0;out_max=1
=>  f(x) = (x+1)/2
diff_temp = (target_temp_high + target_temp_low)/2 - current_temp
=> round(((diff_temp+1)/2)/0.1)*0.1;
```
I use that formula for 2 years and it works great, is easy to understand and fast to compute.

For temperature fine tuning, I've tested [PID climate controller](https://en.wikipedia.org/wiki/PID_controller#Integral_term), but my low temperature floor heating has too much inertia to find good values for ki, kp ,kd

The next step I'll go is to fine tune the target valve values with hassio automations. It would be most easy cause hassio retains historical values and can have more sensors, like external temperature, etc.

You can get temperature from external sensors like [Xiaomi BLE](https://esphome.io/components/sensor/xiaomi_ble.html?highlight=xiaomi_lywsdcgq) or via hassio and then compute a [template sensor](https://esphome.io/components/sensor/template.html?highlight=template)

Karl-opec, 2021-11-08:
Hello, great project,

VL means supply flow,
RL means return flow.

I have on my actual Floor Heating system (standard wax based Actuators to control flow) on top of the PWM a PID controller running. Its  PID_PFactor is 0.95, PID_IFactor is 0,59, PID_DFactor =0.5, The D-Value is based on a gradient t(n) to t(n-7) with recalc time of the PID controller of every 60 sec. It works good.  My experience is that the PID controller is needed to keep the Temperature  close to the desired Temp.

nliaudat, 2021-11-08:
They are 7 free pin available to add custom sensors

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

Look at https
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

Look at [schematics.pdf](https://github.com/nliaudat/esp32_8ch_motor_shield/blob/main/PCB/Schematic.pdf) for details.

You can use [NTC sensors](https://esphome.io/components/sensor/ntc.html?highlight=ntc) or values from hassio.

Code need to be rewritten a bit (THx_check), but it's simple task

nliaudat, 2021-11-09:
The new firmware version lets you change the valve position formula (at line 53). You can adapt it to get what you want.
Regards
(https://github.com/nliaudat/esp32_8ch_motor_shield/blob/main/firmware/esphome_firmware_sample.yaml)

nstadigs, 2021-11-10:
Maybe you already know, but apparently esphome has a [PID Climate component](https://esphome.io/components/climate/pid.html) with [support for autotuning](https://esphome.io/components/climate/pid.html#autotuning).

nliaudat, 2021-11-10:
Yes, you can replace thermostat component with PID Climate, I works the same and a sample code is provided in the yaml file (commented out)

nliaudat, 2021-11-10:
Sorry, the code was not fully included :

`climate:
  - platform: pid
    id: office_pid_thermostat
    name: "Office PID climate"
    sensor: Office_temperature
    default_target_temperature: 21°C
    heat_output: output_office_cover
    control_parameters:
      kp: 18
      ki: 2300
      kd: 0.5

output:
  - platform: template
    id: output_office_cover
    type: float
    write_action:
      - cover.control:
            id: CH6_cover
            position: !lambda return state;
      - logger.log:
            format: "CH6 moved to position %.1f"
            args: [ 'state' ]       `

I have test the climate component, but the update frequency is to hight for valve good life

heinemannj, 2023-09-29:
Is it also possible to use 12 x 1-wire temperature sensors (DS18B20) connected to your board?

I've already implemented via espHome with
[Smart Thermostat with auto Heat/Cool mode, PID control and PWM (Home Assistant component)](https://github.com/hacker-cb/hassio-component-smart-thermostat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) and this working fine with my actual ON/OFF Actuators.

But I want to change to Homematic valve actuators [HmIP-VDMOT] for some reasons ;-)

nliaudat, 2023-09-29:
Yes, you only need a VCC, GND, IO.
All is available in https://github.com/nliaudat/esp32_8ch_motor_shield/blob/main/extension.md

heinemannj, 2023-10-02:
Coming back to the origional topic: **thermal balancing**

In Germany, a hydraulic balancing must be carried out after installation or changes to a heating system.

However, if the heating circuit conditions like line cross-sections and line lengths of the individual heating circuits are not known, an exact calculation of the required flow rate is not possible.

For this reason, only a thermal calibration can be carried out.

By measuring the supply flow temperature and the return flow temperature in each individual heating circuit, you can calculate the spread.

Ideally the spread in each heating circuit within one thermal zone (e.g. room) should be equal.

For the thermal calibration you have three possibilities:

1. Adjust the flow via your flow meters
2. Adjust the flow via proportional valve actuators
3. Adjust initially via flow meters and then daily on demand based on room and outside temperature conditions via proportional valve actuators

The third is obviously the best method because then you have setup a real `dynamic hydraulic balancing.`

As mentioned by [Karl-opec](https://github.com/Karl-opec) an external HA PID controller can manage this (please see above).

It is also mentioned in [floor-heating-controller](https://github.com/nliaudat/floor-heating-controller) wiki that you can use Hassio custom climate components.

Can you please provide some example code for the usage/integration of Hassio components to control the valve percentage of the actuators.

nliaudat, 2023-10-02:
There is 2 ways to go to do external PID control :

The simplest is to adjust the target temperature (like in https://github.com/KartoffelToby/better_thermostat)
The second is to control valves motors and then use the "motor firmware", but I have no experiences in that way.

nliaudat, 2023-10-02:
https://github.com/vindaalex/multizone-thermostat can control proportionnal valves

heinemannj, 2023-10-13:
I've setup an very early alpha version of a documentation / project paper to describe the goals and the physics behind:

https://github.com/heinemannj/Hydraulic-Balancing/edit/main/README.md

Closed 2024-02-24.

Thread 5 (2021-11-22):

Move the rj11 connectors a little bit over the edge of the board

nstadigs, 2021-11-22:
<!-- READ THIS FIRST:
 - This is for feature requests only, for issues please go to the issues repository.
 - Please be as descriptive as possible, especially use-cases that can otherwise not be solved boost the problem's priority.

 DO NOT DELETE ANY TEXT from this template! Otherwise the issue may be closed without a comment.
-->

It would be great if the connectors stuck out from the board by a couple of millimeters.
<!-- A description of what you want to happen. -->

**Please describe your use case for this integration and alternatives you've tried:**
<!-- A clear and concise description of what the problem is. -->

I wanted to create a custom 3d printed box for my two boards with individual holes for the separate rj11 connectors, but it's hard to do when they are aligned with the edge of the board.

**Additional context**
<!-- Add any other context about the feature request here. -->

<!-- LEAVE THIS LINE AS-IS AND DON'T DELETE IT, OTHERWISE THE FEATURE REQUEST WILL BE CLOSED AUTOMATICALLY. -->

nliaudat, 2021-11-22:
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

There is a track for connecting motors without an RJ45 connector which is at the edge of the board and which locks the location of the RJ45 connector. I'll do some tests to move it, but in the meantime the easiest way is to cut the board.

nstadigs, 2021-11-22:
Oh, that's great to hear! Then I'll just cut it :)

Thanks!

nliaudat, 2021-11-23:
done in v53 release

Closed 2021-11-23.

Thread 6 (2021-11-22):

ESP hangs and L9110S gets very warm

nstadigs, 2021-11-22:
Hi!

I understand if this isn't a support channel for newbies like me, but I'm desperate so I'll give it a try anyhow.

I ordered a couple of boards from jlcpcb with chips assembled. The only change I made was selecting [this L9110S](https://jlcpcb.com/parts/componentSearch?isSearch=true&searchTxt=C85174) instead of the [one in the BOM](https://jlcpcb.com/parts/componentSearch?isSearch=true&searchTxt=C85174), because that one was out of stock for several months. They seemed compatible, but again, I'm new to this.

I did not have any issues soldering the through hole components and I have tested all the joints.

The issue: The L9110S runs warm and the motors are supplied constant voltage of 1.3 volts, even when there is no ESP connected to the board.

Did I select an incompatible L9110S? Do you have any troubleshooting tips :grimacing:

Thanks :pray:

PS: If you were to sell ready-made boards I'd buy two of them ;)

nliaudat, 2021-11-22:
Which motor do you use ?
Have you a 3.3V power source and a multimeter to make tests ?
The only difference I see with the original chip is the max voltage supported 12V for mine and 7V for yours
I mean a 10K resitor is broken or not good soldered

With the EPS not connected to the shied, are the motor running on each 8 channels ?

nstadigs, 2021-11-22:
> Which motor do you use ?

HmIP-VDMOT

> Have you a 3.3V power source...

I have and HLK-5M03 soldered to the board and the backside of the board secured.

> ...and a multimeter to make tests ?

Sure do!

> The only difference I see with the original chip is the max voltage supported 12V for mine and 7V for yours

Sounds promising, thanks

> I mean a 10K resitor is broken or not good soldered

Ok..

> With the EPS not connected to the shied, are the motor running on each 8 channels ?

Yes, its running on each channel

nliaudat, 2021-11-22:
I'll do some tests this evening, but the BEMF (back electromotive force) should be 0 cause no motor is connected.
Is the ESP connected or not ? Perhaps it's a faulty SN74HC595 shift register
Can you put a picture of the front and the back of your board ? I'll check the soldering

nliaudat, 2021-11-22:
Are the L9110S chips turned correctly in the right direction ?
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

nstadigs, 2021-11-22:
The esp isn't connected.

The the point on the L9110S is next to the point on the board. Lower left .

Thanks! I'll send you some pictures later

nstadigs, 2021-11-22:
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

nliaudat, 2021-11-22:
Have you jumper cables ?

Can you check the motor voltage if you link IA to GND and IB to VCC, and after that IA to VCC and IB to GND.
Values should be + or - 3.3V
Test only on channel 1
(they are many holes labeld VCC and GND on the board)

nliaudat, 2021-11-22:
Some of your soldering are very bad.
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

All soldering must be disconnected, chrome and brilliant (not dull nor yellowed). Sorry for my bad english :(

nliaudat, 2021-11-22:
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

nstadigs, 2021-11-22:
2.2 volts and 1.7 volts

Yeah, I figured my soldering wasn't the best. But I thought it would be good enough :)
I'll try to fix it to see if that fixes the problem.

Thanks again!

nliaudat, 2021-11-22:
I've reproduced your problem inverting the L9110s module upside down. I've got the same results.

I can send you 2x v1.0 prototype boards and you send me back 2 of your to do more checks if you want.

Closed 2021-11-22.

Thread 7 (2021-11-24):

[FEATURE REQUEST] Use an external power adapter?

nstadigs, 2021-11-24:
<!-- READ THIS FIRST:
 - This is for feature requests only, for issues please go to the issues repository.
 - Please be as descriptive as possible, especially use-cases that can otherwise not be solved boost the problem's priority.

 DO NOT DELETE ANY TEXT from this template! Otherwise the issue may be closed without a comment.
-->

**Describe the problem you have/What new integration you would like**
<!-- A description of what you want to happen. -->

If you would add support for using an external power adapter then the users would not have to deal with mains power. I do think that installing this legally in some countries would actually require a certified electrician if that's even allowed without CE mark.

**Please describe your use case for this integration and alternatives you've tried:**
<!-- A clear and concise description of what the problem is. -->

**Additional context**
<!-- Add any other context about the feature request here. -->

<!-- LEAVE THIS LINE AS-IS AND DON'T DELETE IT, OTHERWISE THE FEATURE REQUEST WILL BE CLOSED AUTOMATICALLY. -->

nstadigs, 2021-11-24:
Sorry, I just realized that you fixed this in 1.4 :man_facepalming:

nliaudat, 2021-11-24:
You can already use some external power adapter like [that one](https://fr.aliexpress.com/item/32968108837.html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).
Everything with 3.3V and 1.25 A (~ 4 Watt) can do the job.
The price is ~3x greater than HLK-5M03.
You have to link it with any of the VCC-GND pin labeled on the board.

nstadigs, 2021-11-24:
You're totally right. I was posting before thinking. I was thinking about an actual connector on the board. But I could just make a hole in the box for a [connector like this](https://www.amazon.se/dp/B07N7G7MCP/ref=sr_1_3?keywords=dc+honkontakt&qid=1637741353&sr=8-3) and connect my two boards to that connector in parallel on the inside.

nliaudat, 2021-11-24:
Usually, there is no power source in the valve manifolds location. You must disconnect an existing 230V valve and wire it to the board. That's the why the external power was not a solution.

You can use a 230V power socket like that
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

nstadigs, 2021-11-24:
Interesting. I have a standard EU plug like this so I though it was common. I know other houses around here have the same solution. The Uponor controller, which most people pick around here has a standard plug for it:

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

Closed 2021-11-24.

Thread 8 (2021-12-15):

In the latest version + and - are connected

nstadigs, 2021-12-15:
<!-- Thanks for reporting a bug for this project. READ THIS FIRST:

- Provide as many details as possible. Simply saying "X gives bug" or "X gives error" is not enough!
- Paste logs, configuration sample and code into the backticks (```).
- Read through the template carefully and fill out all missing details.
- Please also search for similar issues in this issue tracker first and read through the ESPHome FAQ.

DO NOT DELETE ANY TEXT from this template! Otherwise the issue may be closed without a comment.
-->

**Operating environment/Installation (Hass.io/Docker/pip/etc.):**
<!--
Please provide details about your environment below this line. -->
N/A

**ESP (ESP32/ESP8266, Board/Sonoff):**
<!--
Please provide details about which ESP you're using below.
-->
N/A

**ESPHome version (latest production, beta, dev branch)**
<!--
ESPHome version like v1.14 or 1.15-dev
-->
N/A
**Affected component:**
<!--
Please add the link to the documentation at https://esphome.io/index.html of the component in question.
-->
N/A

**Description of problem:**
In the latest version 3.3v and ground are connected

**Problem-relevant YAML-configuration entries:**
```yaml
PASTE YAML FILE HERE

```

**Logs (if applicable):**
<!--
Please copy the debug log here. If possible, also connect to the ESP over USB and copy those logs into the backticks.
-->
```
PASTE DEBUG LOG HERE

```

**Additional information and things you've tried:**

It's probably this, right?

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

<!-- LEAVE THIS LINE AS-IS AND DON'T DELETE IT, OTHERWISE THE ISSUE WILL BE CLOSED AUTOMATICALLY. -->

nliaudat, 2021-12-16:
I see.
Can you send the part number of the HLK 3.3V power supply.

nstadigs, 2021-12-16:
It's the HLK-5M03 provided in the BOM file: C209906

nstadigs, 2021-12-16:
To clarify, they are connected even on a bare board with nothing soldered

nstadigs, 2021-12-16:
I should be able to just drill out these VCC holes to see if that fixes the problem, right? If so, I can just connect the 3.3v elsewhere with a cable. What do you think?

nstadigs, 2021-12-16:
I can confirm that this solved the issue
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

nliaudat, 2021-12-30:
Sorry for that issue. The HLK footprints were wrong. I'll add extra space in next release

nliaudat, 2021-12-30:
Fixed in release V54

Closed 2021-12-30.

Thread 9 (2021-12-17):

Unable to read BEMF

nstadigs, 2021-12-17:
<!-- Thanks for reporting a bug for this project. READ THIS FIRST:

- Provide as many details as possible. Simply saying "X gives bug" or "X gives error" is not enough!
- Paste logs, configuration sample and code into the backticks (```).
- Read through the template carefully and fill out all missing details.
- Please also search for similar issues in this issue tracker first and read through the ESPHome FAQ.

DO NOT DELETE ANY TEXT from this template! Otherwise the issue may be closed without a comment.
-->

**Operating environment/Installation (Hass.io/Docker/pip/etc.):**
<!--
Please provide details about your environment below this line. -->
pip
**ESP (ESP32/ESP8266, Board/Sonoff):**
<!--
Please provide details about which ESP you're using below.
-->
ESP32-DevKitC-v4
**ESPHome version (latest production, beta, dev branch)**
<!--
ESPHome version like v1.14 or 1.15-dev
-->
ESPHome version 2021.12.1
**Affected component:**
<!--
Please add the link to the documentation at https://esphome.io/index.html of the component in question.
-->
adc

**Description of problem:**
ADC sensor senses nothing even tho I get small values when measured at the pins.

**Problem-relevant YAML-configuration entries:**
```yaml
esphome:
  name: floor-heating-controller-1
  platform: ESP32
  board: nodemcu-32s

wifi:
  networks:
  - ssid: !secret wifi_ssid_1
    hidden: true
    password: !secret wifi_password_1
    priority : 1

mqtt:
  broker: 192.168.0.186

ota:

web_server:
  port: 80

sn74hc595:
  - id: 'sn74hc595_hub'
    data_pin: GPIO16 #Pin connected to SN74HC595 SER input
    clock_pin: GPIO5 #Pin connected to SN74HC595 SRCLK pin
    latch_pin: GPIO17 #Pin connected to SN74HC595 RCLK pin
    oe_pin: GPIO18 ### needed by esphome, but connected to GND (outputEnable is used only for pwm all th pin)
    sr_count: 2 #Number of daisy-chained shift registers, up-to 4

# Enable logging
logger:
  level: DEBUG #NONE# ERROR #INFO #DEBUG  #VERBOSE
  baud_rate: 0 #to disable logging via UART
  logs:
    adc: INFO

switch:
    ### CH1
  - platform: gpio
    name: "CH1 IA"
    pin:
      sn74hc595: sn74hc595_hub
      number: 0
      inverted: False
    internal: false
    id: CH1_IA_pin
    interlock: &interlock_group_CH1 [CH1_IA_pin, CH1_IB_pin]
    restore_mode: always off
  - platform: gpio
    name: "CH1 IB"
    pin:
      sn74hc595: sn74hc595_hub
      number: 1
      inverted: False
    internal: false
    id: CH1_IB_pin
    interlock: *interlock_group_CH1
    restore_mode: always off

sensor:
  - platform: adc
    id : BEMF_1_2_sensor_ADC
    pin: GPIO36
    name: "BEMF 1" #CH1 + CH2
    update_interval: 500ms
    attenuation : 2.5db

```

**Logs (if applicable):**
<!--
Please copy the debug log here. If possible, also connect to the ESP over USB and copy those logs into the backticks.
-->
```
[09:24:25][D][sensor:113]: 'BEMF 1': Sending state 0.07800 V with 2 decimals of accuracy
[09:24:25][D][sensor:113]: 'BEMF 1': Sending state 0.07800 V with 2 decimals of accuracy
[09:24:26][D][sensor:113]: 'BEMF 1': Sending state 0.07800 V with 2 decimals of accuracy
[09:24:26][D][switch:021]: 'CH1 IA' Toggling ON.
[09:24:26][D][switch:037]: 'CH1 IA': Sending state ON
[09:24:26][D][sensor:113]: 'BEMF 1': Sending state 0.07800 V with 2 decimals of accuracy
[09:24:27][D][sensor:113]: 'BEMF 1': Sending state 0.07800 V with 2 decimals of accuracy
[09:24:27][D][sensor:113]: 'BEMF 1': Sending state 0.07800 V with 2 decimals of accuracy
[09:24:28][D][sensor:113]: 'BEMF 1': Sending state 0.07800 V with 2 decimals of accuracy
[09:24:28][D][switch:021]: 'CH1 IA' Toggling OFF.
[09:24:28][D][switch:037]: 'CH1 IA': Sending state OFF
[09:24:28][D][sensor:113]: 'BEMF 1': Sending state 0.07800 V with 2 decimals of accuracy
[09:24:29][D][sensor:113]: 'BEMF 1': Sending state 0.07800 V with 2 decimals of accuracy
[09:24:29][D][switch:021]: 'CH1 IB' Toggling ON.
[09:24:29][D][switch:037]: 'CH1 IB': Sending state ON
[09:24:29][D][sensor:113]: 'BEMF 1': Sending state 0.07800 V with 2 decimals of accuracy
[09:24:30][D][sensor:113]: 'BEMF 1': Sending state 0.07800 V with 2 decimals of accuracy
[09:24:30][D][sensor:113]: 'BEMF 1': Sending state 0.07800 V with 2 decimals of accuracy
[09:24:31][D][sensor:113]: 'BEMF 1': Sending state 0.07800 V with 2 decimals of accuracy
[09:24:31][D][sensor:113]: 'BEMF 1': Sending state 0.07800 V with 2 decimals of accuracy
[09:24:31][D][switch:021]: 'CH1 IB' Toggling OFF.
[09:24:31][D][switch:037]: 'CH1 IB': Sending state OFF
[09:24:32][D][sensor:113]: 'BEMF 1': Sending state 0.07800 V with 2 decimals of accuracy
[09:24:32][D][sensor:113]: 'BEMF 1': Sending state 0.07800 V with 2 decimals of accuracy
[09:24:33][D][sensor:113]: 'BEMF 1': Sending state 0.07800 V with 2 decimals of accuracy
[09:24:33][D][sensor:113]: 'BEMF 1': Sending state 0.07800 V with 2 decimals of accuracy
```

**Additional information and things you've tried:**

Board: v53 rev 1.19

Putting a multimeter between GPIO36 and GND gives around 20mV when the motor is running unhindered and around 50mV at end stops. Are these values normal?
If I set the ADC sensor to report "raw" I get only 0's. As I understand I should get a value between 0 and 4096.
Maybe these values are too low to be measured by my esp32? Or are the values from my board lower than expected?

I've tried other pins and motor contacts but with the same results.

PS. I haven't received the old board you sent me yet, but I payed the import taxes for them yesterday. The local postal service had entered the wrong address for the payment notice letter so it was brought here by my neighbor.  So they will probably arrive soon. Thanks again :)

EDIT:

I've also tried this with the same results:
```
esp32:
  board: nodemcu-32s
  framework:
    type: arduino #esp-idf  not ready missing json and async_tcp
    version: recommended #latest
```

This seems to be the legacy way to specify the board, and json and async_tcp are now working with esp-idf using the newer configuration method that I posted originally.

<!-- LEAVE THIS LINE AS-IS AND DON'T DELETE IT, OTHERWISE THE ISSUE WILL BE CLOSED AUTOMATICALLY. -->

nliaudat, 2021-12-17:
Please try to set `attenuation: auto`
[ADC sensor](https://esphome.io/components/sensor/adc.html) change in 2021.11 esphome release.
My Esp32 works great with 2021.11 release but it depends on manufacturer calibration

nstadigs, 2021-12-17:
Thanks, I've tried that. That seems to set it to 2.5db automatically, giving the same values.:
```
[10:01:45][D][sensor:113]: 'BEMF 1': Sending state 0.07500 V with 2 decimals of accuracy
[10:01:45][D][switch:021]: 'CH1 IB' Toggling ON.
[10:01:45][D][switch:037]: 'CH1 IB': Sending state ON
[10:01:45][D][sensor:113]: 'BEMF 1': Sending state 0.07500 V with 2 decimals of accuracy
[10:01:46][D][sensor:113]: 'BEMF 1': Sending state 0.07500 V with 2 decimals of accuracy
[10:01:46][D][sensor:113]: 'BEMF 1': Sending state 0.07500 V with 2 decimals of accuracy
[10:01:46][D][switch:021]: 'CH1 IB' Toggling OFF.
[10:01:46][D][switch:037]: 'CH1 IB': Sending state OFF
[10:01:47][D][sensor:113]: 'BEMF 1': Sending state 0.07500 V with 2 decimals of accuracy
[10:01:47][D][sensor:113]: 'BEMF 1': Sending state 0.07500 V with 2 decimals of accuracy
```

nliaudat, 2021-12-17:
ADC values are proportional to vref (esp32 input voltage). Can you check input voltage ?

nstadigs, 2021-12-17:
Input is 3.30 V
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
nliaudat, 2022-02-13:
Many thanks for the comment. I did not knew the https://github.com/Lenti84/VdMot_Controller project.
I work on a complete refractor of the project with custom valves as the homematic Vmot are bad quality (they jump around their support and breaks).
What is your recommendation for the resistors value ? I've made many tests and the best is 12kohm in series but L9110s chip is not well documented and interfering

nstadigs, 2022-02-14:
> Many thanks for the comment. I did not knew the https://github.com/Lenti84/VdMot_Controller project. I work on a complete refractor of the project with custom valves as the homematic Vmot are bad quality (they jump around their support and breaks). What is your recommendation for the resistors value ? I've made many tests and the best is 12kohm in series but L9110s chip is not well documented and interfering

I too have been thinking about custom valve motors for some time. I started experimenting with a custom ESPhome component for your board that counts motor revelations with code borrowed from https://github.com/Lenti84/VdMot_Controller. But the values from the BEMF relies on the amount of pressure caused by your specific valve pins, so that gets pretty complex. So instead I started to look into using stepper motors for driving the valves. I found these [small 5v stepper motors with integrated reducing gears and a 3m thread in the pin](https://www.aliexpress.com/item/32797216294.html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) on AliExpress. I'm thinking that if you put an M3 hex head screw in the hole in the pin and lock the rotation of the screw you can use that to press the pin. This would allow fine grained positioning of the valve without constant recalibration. What do you think?

nliaudat, 2022-02-14:
I've made a working valve with https://fr.aliexpress.com/item/4000311295036.html?spm=a2g0s.12269583.0.0.18834b0ejbgKSj
15 RPM, 3V.

For steppers, a lot a TRV valve manufacturers use https://www.alibaba.com/product-detail/Brand-new-Linear-actuator-for-Valve_60637359967.html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

Steppers is a good solution for position handling, but do not survive a controller reboot (lost position value).

I work on an absolute position control with a reflective optical sensor (ITR8307). That means the controller board must read one more analog input for each valve. The ESP32 is limited in ADC and that involve to use a analog multiplexer (CD74HC4067).

nstadigs, 2022-02-14:
> I started experimenting with a custom ESPhome component for your board that counts motor revelations with code borrowed from https://github.com/Lenti84/VdMot_Controller. But the values from the BEMF relies on the amount of pressure caused by your specific valve pins, so that gets pretty complex.

I was thinking about using a small push button on the top side to determine the top position at startup. This is similar to what 3d-printers do.

> I work on an absolute position control with a reflective optical sensor (ITR8307). That means the controller board must read one more analog input for each valve. The ESP32 is limited in ADC and that involve to use a analog multiplexer (CD74HC4067).

Very interesting! I'm eager to see what you come it with :)

nliaudat, 2022-03-16:
For information, I upgraded today from python 3.7 to 3.10.3 and recompile with latest esphome and now the null value of BEMF sensor is 0.08V instead of 0.0V
Very strange .... I'll investigate if I'll find time to.

dragop4, 2022-12-20:
@nliaudat do you have any solution about this?
I started with this project, build and installed to esp directly from esphome dashboard (Homeassistant). And i have permanent  0.08 V  on BEMF sensor.
1.35 v54 board version, ESP32-WROOM-32U chip and HmIP-VDMOT actuators.

nliaudat, 2022-12-20:
@dragop4  No solution for 0.08V reading.
I mean it's related to python 3.8 rounding number changes.
Reading ADC 0.08 means 0V and that's not a problem to upper the BEMF trigger by 0.1

The latest board as opamp to have better ADC reading.

dragop4, 2022-12-21:
>

it's possible to modify my board without ordering new?

nliaudat, 2022-12-21:
have a look at https://github.com/nliaudat/esp32_8ch_motor_shield/discussions/19#discussioncomment-3724593

Closed 2021-12-30.

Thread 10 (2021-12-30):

Order possibilities ?

marcelveldt, 2021-12-30:
Hi! This project looks really interesting and I've been looking for something like this for a while now.
I actually own the Homematic IP actuators etc. but not very happy with it.
Are there any possibilities to order 2 prebuilt actuators/shields ?

nliaudat, 2021-12-30:
Hi, the project is still in early development. No order possibilities actually. Sorry

nliaudat, 2021-12-30:
You can order at JLPCB or other PCB manufacturer

marcelveldt, 2021-12-30:
Thanks for the reply!
I'll wait until it is in final shape then.

nethawk2, 2022-01-15:
Hi Nicolas, i would like to order at JLCPCB, they want a gerber file. Can you provide your gerber file for upload to JLCPCB ?
Tahnk you

nliaudat, 2022-01-15:
All you need is in the release (https://github.com/nliaudat/esp32_8ch_motor_shield/releases)

nethawk2, 2022-01-16:
Thank you.
One part seems not available for a longer time: JLCPCB Part Nr. C273642, TI SN74HC595PWR
Do you have a suggestion for a replacement ?
Thank you

nstadigs, 2022-01-16:
Hi @nethawk2. That part seems to get in and out of stock frequently. I suggest that you try again in a couple of days. I suspect that this is a result of the global chip shortage.

nethawk2, 2022-01-16:
Thx @nstadigs , on other webpages i saw a schedule of 10 months or even 2023.

I am really not the hardware guy, but i try to learn.
Would Texas Instruments SN74HC595DRG3 , JLCPCB Part Nr. C94270 be a good replacement ?

nliaudat, 2022-01-16:
Not compatible, you must find any SN74HC595 part with the same sock (TSSOP-16). I advise you to wait a week. LCSC has a stock of 2000+

nethawk2, 2022-01-17:
How about 74HC595T16-13 from Diodes Incorporated , Part Nr. C148115 ?
This is my last try to find a substitute to not waste more of your time.

nliaudat, 2022-01-18:
1st : do not write in closed issues.
2nd : that's not an issue
3rd : You can wait for JLCPCB to have stock or find another PCB manufacturer

Closed 2021-12-30.

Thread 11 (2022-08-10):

H1 H3 cannot match the corresponding pads on the PCB board

flexmatics, 2022-08-10:
Hey,

Ordered PCB using the files here: https://github.com/nliaudat/esp32_8ch_motor_shield/releases/tag/v54

JCB gave this reply:
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

Deselected these parts as didn't know what to do - did I mess up or can still expect to get working board?
Corrected PDF from JCB should look like this:
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

Thanks.

nliaudat, 2022-08-11:
Hi,
H1 and H3 are only mounting holes. You can delete them safely.
I've ordered many time that PCB and they never complain ...
H1 and H3 have enough space in easyeda.
Regards

Closed 2022-08-11.

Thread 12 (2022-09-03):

Not an issue: I will have 6 assembled boards available for german buyers...

Lonestar78, 2022-09-03:
Dear All,

not exactly an issue ;-)
i just ordered 10 assembled PCBs and can make 6 available for buyers (cheapest shipping in Germany)
Let me know if interessted.

Kind regards
Christian

ChristianBuer, 2022-09-09:
Hi,
I am interested. How much would three of them cost with shipping in Germany (I live in Wuppertal).

Kind regards,
Christian

Lonestar78, 2022-09-10:
Hi, I would say about 22 € per assembled PCB plus DHL. The delivery should be at my door next week.
Kind regards Christian

Holen Sie sich Outlook für Android<https://aka.ms/AAb9ysg>
________________________________
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

linuxdep, 2022-09-10:
Hi, schön, ich hätte auch Interesse an 2 PCB's. Ist der ESP32 auch dabei?

Lonestar78, 2022-09-10:
Hi, would be without the ESP32, but i need to check how many i ordered on ali ;-)
If both above tke the PCBs i would have 2 more to offer.
which forum are you in? I can generate an account there.

linuxdep, 2022-09-10:
https://homematic-forum.de/forum/
Da passt es ja hin...

Lonestar78, 2022-09-10:
done... same username as on git

danif86, 2022-09-11:
I need 3, only 1 left? And live in Norway (would pay for shipping)

nliaudat, 2022-09-11:
Hi, I've created a discussion to buy or sell boards :
https://github.com/nliaudat/esp32_8ch_motor_shield/discussions/categories/buy-or-sell

playya, 2022-09-18:
@Lonestar78 I need only a single board and as a software guy to dump to order at JLCPCB.
Is the last board still available?

Closed 2022-09-11.

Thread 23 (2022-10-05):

SCREW_HOLE_GROUD

WMP, 2022-10-05:
Hell, i want  to order this PCB on JLCPCB, but there isnt SCREW_HOLE_GROU available.

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

Do you know how to found this part in JLCPCB?

nliaudat, 2022-10-05:
Hi, this is not a part. That's screw holes. I mean you can ignore it

WMP, 2022-10-05:
Thank you, that's what I thought but I preferred to make sure.

Closed 2022-10-05.

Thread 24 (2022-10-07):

[FEATURE REQUEST] Create new board to connect DHTxx or DS18B20 thermometers.

WMP, 2022-10-07:
<!-- READ THIS FIRST:
 - This is for feature requests only, for issues please go to the issues repository.
 - Please be as descriptive as possible, especially use-cases that can otherwise not be solved boost the problem's priority.

 DO NOT DELETE ANY TEXT from this template! Otherwise the issue may be closed without a comment.
-->

**Describe the problem you have/What new integration you would like**
I have a house in which each room has two RJ45 jacks in the wall. In one socket I always have a DS18B20 or DHT11/22 temperature sensor, and the other is a regular Ethernet. Currently, I have spaghetti-style cables connected in the patchpanel and connected to the esp8266 wroom. This is extremely ugly and hard to maintain and service. I wanted to create a board in easyPSB that would end the mess, but I have absolutely no knowledge of the subject, and this would be my first board. That's why I thought you might want to implement my idea.

**Please describe your use case for this integration and alternatives you've tried:**
The board should have space for esp32/esp8266 wroom, a USB socket for power, and be surrounded by RJ45 sockets.  Each socket should be labeled with which GPIO port it is plugged into.

There should be two jumpers at each socket:
One should select whether a One-Wire or DHTxx sensor is plugged into the port. If the jumper is set to One-Wire mode, then one of the wires of the RJ45 connector should be connected to the GPIO port of your choice on the ESP wroom. Of course, all RJ45 jacks set to One-Wire should be connected to the same GPIO port, and there should be a 4.7kOHM resistor between the "One-Wire bus" and the GPIO port.

Setting to DHTxx mode should connect one wire to a separate GPIO port. DHT requires a 10kOhm resistor, but because of the distance, a different resistor may work better. I don't know if it is a good idea to install a 10kOhm resistor for each socket. or are there adjustable resistors? Each socket should have a separate GPIO port.

However, there are cases when there are too many DS18B20s plugged into one GPIO port. I think then you can set a jumper to DHTxx mode and have a separate One-Wire bus to such a port.

The other jumper should set a voltage of 3.3V or, for a longer distance 5V. Since the ESP does not have a 5V power supply, you would have to take it directly from the USB socket.

**Additional context**
<!-- Add any other context about the feature request here. -->
Multiple DHTxx wiring:
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
Multiple DS18B20 wiring:
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

<!-- LEAVE THIS LINE AS-IS AND DON'T DELETE IT, OTHERWISE THE FEATURE REQUEST WILL BE CLOSED AUTOMATICALLY. -->

nliaudat, 2022-10-08:
The actual board is a dev board with many free gpio available for [extensions](https://github.com/nliaudat/esp32_8ch_motor_shield/blob/main/extension.md).

You could modify as you want, add more sensors with the free gpios. If you need RJ45 socket and custom integration without the knowledge to add it yourself, you are in the wrong place.

Regards

Closed 2022-10-08.

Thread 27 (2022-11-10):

[BUG] CH6 input shorted to CH7/8 BEMF

microtronics, 2022-11-10:
<!-- Thanks for reporting a bug for this project. READ THIS FIRST:

- Provide as many details as possible. Simply saying "X gives bug" or "X gives error" is not enough!
- Paste logs, configuration sample and code into the backticks (```).
- Read through the template carefully and fill out all missing details.
- Please also search for similar issues in this issue tracker first and read through the ESPHome FAQ.

DO NOT DELETE ANY TEXT from this template! Otherwise the issue may be closed without a comment.
-->

**Operating environment/Installation (Hass.io/Docker/pip/etc.):**
<!--
Please provide details about your environment below this line. -->

**ESP (ESP32/ESP8266, Board/Sonoff):**
<!--
Please provide details about which ESP you're using below.
-->

**ESPHome version (latest production, beta, dev branch)**
<!--
ESPHome version like v1.14 or 1.15-dev
-->

**Affected component:**
<!--
Please add the link to the documentation at https://esphome.io/index.html of the component in question.
-->
V54r1.35 Board

**Description of problem:**
The via shorts CH6 input to CH7/8 bemf
Didn't the DRC show this error?
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

**Problem-relevant YAML-configuration entries:**
```yaml
PASTE YAML FILE HERE

```

**Logs (if applicable):**
<!--
Please copy the debug log here. If possible, also connect to the ESP over USB and copy those logs into the backticks.
-->
```
PASTE DEBUG LOG HERE

```

**Additional information and things you've tried:**

<!-- LEAVE THIS LINE AS-IS AND DON'T DELETE IT, OTHERWISE THE ISSUE WILL BE CLOSED AUTOMATICALLY. -->

nliaudat, 2022-11-10:
Many thanks, fix is done.

Closed 2022-11-12.

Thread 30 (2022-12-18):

[BUG] USB and DC power supply separation by diode

WMP, 2022-12-18:
<!-- Thanks for reporting a bug for this project. READ THIS FIRST:

- Provide as many details as possible. Simply saying "X gives bug" or "X gives error" is not enough!
- Paste logs, configuration sample and code into the backticks (```).
- Read through the template carefully and fill out all missing details.
- Please also search for similar issues in this issue tracker first and read through the ESPHome FAQ.

DO NOT DELETE ANY TEXT from this template! Otherwise the issue may be closed without a comment.
-->

**Operating environment/Installation (Hass.io/Docker/pip/etc.):**
<!--
Please provide details about your environment below this line. -->

**ESP (ESP32/ESP8266, Board/Sonoff):**
<!--
Please provide details about which ESP you're using below.
-->

**ESPHome version (latest production, beta, dev branch)**
<!--
ESPHome version like v1.14 or 1.15-dev
-->

**Affected component:**
<!--
Please add the link to the documentation at https://esphome.io/index.html of the component in question.
-->

**Description of problem:**
If a person who will not be familiar with this board/project will think that because it's a USB it can be plugged into the computer, and the board will be powered from DC it will burn the USB in the computer. Could you add protection, such as diode separation?

In addition, the LDO BL1084-33-CY can heat up when the voltage is higher than 9V, can you for the VCC pin give a copper bond to transfer the heat?

**Problem-relevant YAML-configuration entries:**
```yaml
PASTE YAML FILE HERE

```

**Logs (if applicable):**
<!--
Please copy the debug log here. If possible, also connect to the ESP over USB and copy those logs into the backticks.
-->
```
PASTE DEBUG LOG HERE

```

**Additional information and things you've tried:**

<!-- LEAVE THIS LINE AS-IS AND DON'T DELETE IT, OTHERWISE THE ISSUE WILL BE CLOSED AUTOMATICALLY. -->

nliaudat, 2022-12-19:
Good idea ! Many thanks for the improvements proposal.

I have no time to do it actually, and the DC version was never proper tested as nobody use it.
I mean the DC version will disappear soon :(

WMP, 2022-12-19:
I thinks that 230v AC version is not updated, and recently version is usb or DC. I waiting for new version with fix BEMF, and I want order PCB, what version I should order? 230AC or usb/DC?

nliaudat, 2022-12-19:
The AC version PCB v55 rev 1.45 was tested 4 days ago  https://github.com/nliaudat/esp32_8ch_motor_shield/discussions/19#discussioncomment-4412833

Closed 2023-03-03.

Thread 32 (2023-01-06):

Need help

uplight-dev, 2023-01-06:
Could you help me understand how to order this board from https://jlcpcb.com ?
I saw the Release files are not available anymore.

Thanks!

nliaudat, 2023-01-06:
You can order after connection at [easyeda.com](https://u.easyeda.com/join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). The project is now public

uplight-dev, 2023-01-06:
Thank you!

I tried to order by generating Gerber, BOM, CPL files but at jlcpcb.com I get these errors:
- HLK-5M03 inventory shortage
-  U1 and H1,H3 are missing, cannot be identified; these are provided by Jayesh Prajapati and chan48969999. There's no link in the BOM file for them

Could I go ahead and order without these 3 components and buy them separately and solder them myself?

I found HLK-5M03 here:
https://www.tinytronics.nl/shop/en/power/power-supplies/3.3v/hi-link-pcb-power-supply-3.3vdc-1.5a-hlk-5m03

Thanks!

nliaudat, 2023-01-06:
You can replace the HLK-5M03  with HLK-PM03 (add to bom properties). It's the same with less power. You do not need power if many valves runs at the same time which is not the default config.

U1 is the esp32 dev board, you need to buy it aparts.
Someone changes it to "add in the Bom". I revert that. (that's why I do not make the project public in early steps)

Regards

uplight-dev, 2023-01-06:
One thing I missed to ask, would this board work with a Raspberry PI with a wired connection?
Or can the antenna be used with Raspberry PI?
I don't want to use a wifi connection with it.

nliaudat, 2023-01-06:
No way, wifi only.
That's an esp32 board.

If you have a raspi, why do you want an esp32 shield ? You should find a 8 channel motor driver for rpi.

You could use the RX/TX port to send command to the board with your raspi, but it's out of support.
Regards

uplight-dev, 2023-01-06:
It's because I'd like to use the HmIP-VDMOT actuators.

nliaudat, 2023-01-06:
take a look at https://github.com/Lenti84/VdMot_Controller as alternative.

uplight-dev, 2023-01-06:
While it's out of support, is there  perhaps some similar product or some raspi tutorial on using/connecting the RX/TX ports?
I ask because I think the https://github.com/Lenti84/VdMot_Controller is closed-source and I'm hoping to be able to modify the board myself a bit before printing it.

Closed 2023-01-06.

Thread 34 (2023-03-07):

[FEATURE REQUEST] DC version

WMP, 2023-03-07:
Do you plan to continue developing the DC version? Unfortunately, the HLK-5M03 power supply has low efficiency.

nliaudat, 2023-03-07:
Hello,

I don't think so because the idea was for me to find contributors.

This not being the case and not having any more time, I think that the DC version will disappear. Anyway, the DC version needed a separate AC power supply.

Personally, I think the HLK-5M03 module has a good price/performance ratio.
You can always skip it and power the board directly with 3.3 or 5V with your own power supply module.

Regards

Closed 2023-03-07.

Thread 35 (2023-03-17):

[BUG] closed source project on github?

QuadCorei8085, 2023-03-17:
What is the point of the project being on github when no sources are available just images?

nliaudat, 2023-03-18:
The sources where deleted last month since nobody helped nor commited any improvement since 2 years.
I pushed the easyeda sources and altium designer in [/pcb](https://github.com/nliaudat/esp32_8ch_motor_shield/tree/main/pcb), but not the shared easyeda project on cloud designer.

Regards

WMP, 2023-04-12:
Could you share PCB for version v57 rev 1.48 ?

nliaudat, 2023-04-12:
> Could you share PCB for version v57 rev 1.48 ?

Why do you want an outdated version ? I'll have to search ...

WMP, 2023-04-12:
Because this is last with rj11, I have 10 PCB and I want to make box for this version

nliaudat, 2023-04-12:
The box is on https://github.com/nliaudat/esp32_8ch_motor_shield/tree/main/box

Here you'll find the board PDF for v57 rev 1.48

[PCB_PCB v57 rev 1.48_2023-04-12.pdf](https://github.com/nliaudat/esp32_8ch_motor_shield/files/11214642/PCB_PCB.v57.rev.1.48_2023-04-12.pdf)

Closed 2023-03-18.

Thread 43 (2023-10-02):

Documentation: Add dimensions of the board and the box

heinemannj, 2023-10-02:
Please add the dimensions of the board and the box in documentation.

The dimensions within
https://github.com/nliaudat/esp32_8ch_motor_shield/blob/main/pcb/Schematic_esp32-8ch-dc-motor-shield_AC_2023-03-18.pdf
confusing me.

Cheers
Joerg

nliaudat, 2023-10-02:
Fixed : https://github.com/nliaudat/esp32_8ch_motor_shield/blob/main/pcb/PCB_PCB%20v58%20rev%201.51_2023-10-02.pdf

Closed 2023-10-02.

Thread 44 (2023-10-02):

Documentation: Difference between Floor heating and Motor control firmware

heinemannj, 2023-10-02:
Please clarify about the differences, the approach and possible use cases for:

**Floor heating** : https://github.com/nliaudat/floor-heating-controller
**Motor control** : https://github.com/nliaudat/esphome-8-ch-motor-controller

Cheers
Joerg

nliaudat, 2023-10-02:
1) Floor heating use the climate components to control motor

2) Motor version is to control any kind of motors, like steppers. You can use the esphome hbridge component.

Closed 2023-10-02.

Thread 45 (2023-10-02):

Documentation: Usage of 1-wire temperature sensors

heinemannj, 2023-10-02:
Usage of 1-wire temperature sensors (DS18B20):
https://esphome.io/components/sensor/dallas.html

_"... The 1-Wire bus ... should have an external pullup resistor of about 4.7KΩ. ..."
"... For this, connect a resistor of about 4.7KΩ between 3.3V and the data pin. ..."
"... Values ± 1KΩ will, in most cases, work fine as well, if you don’t have massively long wires. ..."_

|1-Wire Bus|Board|DS18B20|Resistor|
|---|------|-------|--|
|Power|VCC (3.3. V)|red|~4.7KΩ between Power and Data|
|Ground|GND|black|-|
|Data|IO (e.g. IO22)|yellow|~4.7KΩ between Power and Data|

See:
https://github.com/nliaudat/esp32_8ch_motor_shield/blob/main/extension.md

Note:
With proper and short cabling more than 16 DS18B20 on the same 1-wire bus seems to be possible.

nliaudat, 2023-10-02:
Fix in https://github.com/nliaudat/esp32_8ch_motor_shield/wiki/1%E2%80%90wire-temperature-sensors

Closed 2023-10-02.

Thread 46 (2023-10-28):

BEMF is NOT working

heinemannj, 2023-10-28:
Valves are working but by reaching the endstop point there is more then 10 secs tock tock tock and the valve is pressed from the ventil.

board version  v57 rev 1.48

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

ESPRESSiF
ESP32-WROOM-32D

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

Homematic valve actuators [HmIP-VDMOT]

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

```
INFO ESPHome 2023.10.3
INFO Reading configuration /config/esphome/floor-heating-1.yaml...
WARNING GPIO5 is a Strapping PIN and should be avoided.
Attaching external pullup/down resistors to strapping pins can cause unexpected failures.
See https://esphome.io/guides/faq.html#why-am-i-getting-a-warning-about-strapping-pins
INFO Starting log output from floor-heating-1.local using esphome API
INFO Successfully connected to floor-heating-1.local
[19:13:14][I][app:102]: ESPHome version 2023.10.3 compiled on Oct 27 2023, 17:54:34
[19:13:14][I][app:104]: Project nliaudat.floor-heating-controller version 1.94.dev
[19:13:14][C][logger:416]: Logger:
[19:13:14][C][logger:417]:   Level: DEBUG
[19:13:14][C][logger:418]:   Log Baud Rate: 115200
[19:13:14][C][logger:420]:   Hardware UART: UART0
[19:13:14][C][logger:424]:   Level for 'adc': INFO
[19:13:14][C][logger:424]:   Level for 'dallas.sensor': ERROR
[19:13:14][C][logger:424]:   Level for 'wifi': ERROR
[19:13:14][C][logger:424]:   Level for 'wifi_signal.sensor': ERROR
[19:13:14][C][logger:424]:   Level for 'ota': ERROR
[19:13:14][C][logger:424]:   Level for 'uptime.sensor': ERROR
[19:13:14][C][logger:424]:   Level for 'restart': ERROR
[19:13:14][C][logger:424]:   Level for 'mdns': ERROR
[19:13:14][C][logger:424]:   Level for 'internal_temperature': ERROR
[19:13:14][C][logger:424]:   Level for 'sntp': ERROR
[19:13:14][C][logger:424]:   Level for 'web_server': ERROR
[19:13:14][C][logger:424]:   Level for 'captive_portal': ERROR
[19:13:14][C][logger:424]:   Level for 'api': ERROR
[19:13:14][C][logger:424]:   Level for 'component': ERROR
[19:13:14][C][logger:424]:   Level for 'thermostat.climate': ERROR
[19:13:14][C][logger:424]:   Level for 'template.text_sensor': ERROR
[19:13:14][C][logger:424]:   Level for 'sensor': ERROR
[19:13:14][C][logger:424]:   Level for 'binary_sensor': INFO
[19:13:14][C][logger:424]:   Level for 'cover': INFO
[19:13:14][C][logger:424]:   Level for 'switch': INFO
[19:13:14][C][logger:424]:   Level for 'climate': ERROR
[19:13:14][C][logger:424]:   Level for 'endstop': DEBUG
[19:13:14][C][logger:424]:   Level for 'text_sensor': ERROR
[19:13:14][C][logger:424]:   Level for 'homeassistant.sensor': ERROR
[19:13:14][C][sn74hc595:029]: SN74HC595:
[19:13:14][C][switch.gpio:068]: GPIO Switch 'CH1 IA'
[19:13:14][C][switch.gpio:091]:   Restore Mode: always OFF
[19:13:14][C][switch.gpio:031]:   Pin: 0 via SN74HC595
[19:13:14][C][switch.gpio:033]:   Interlocks:
[19:13:14][C][switch.gpio:037]:     CH1 IB
[19:13:14][C][switch.gpio:068]: GPIO Switch 'CH1 IB'
[19:13:14][C][switch.gpio:091]:   Restore Mode: always OFF
[19:13:14][C][switch.gpio:031]:   Pin: 1 via SN74HC595
[19:13:14][C][switch.gpio:033]:   Interlocks:
[19:13:14][C][switch.gpio:037]:     CH1 IA
[19:13:14][C][switch.gpio:068]: GPIO Switch 'CH2 IA'
[19:13:14][C][switch.gpio:091]:   Restore Mode: always OFF
[19:13:14][C][switch.gpio:031]:   Pin: 2 via SN74HC595
[19:13:14][C][switch.gpio:033]:   Interlocks:
[19:13:14][C][switch.gpio:037]:     CH2 IB
[19:13:14][C][switch.gpio:068]: GPIO Switch 'CH2 IB'
[19:13:14][C][switch.gpio:091]:   Restore Mode: always OFF
[19:13:14][C][switch.gpio:031]:   Pin: 3 via SN74HC595
[19:13:14][C][switch.gpio:033]:   Interlocks:
[19:13:14][C][switch.gpio:037]:     CH2 IA
[19:13:14][C][switch.gpio:068]: GPIO Switch 'CH3 IA'
[19:13:14][C][switch.gpio:091]:   Restore Mode: always OFF
[19:13:14][C][switch.gpio:031]:   Pin: 4 via SN74HC595
[19:13:14][C][switch.gpio:033]:   Interlocks:
[19:13:14][C][switch.gpio:037]:     CH3 IB
[19:13:14][C][switch.gpio:068]: GPIO Switch 'CH3 IB'
[19:13:14][C][switch.gpio:091]:   Restore Mode: always OFF
[19:13:14][C][switch.gpio:031]:   Pin: 5 via SN74HC595
[19:13:14][C][switch.gpio:033]:   Interlocks:
[19:13:14][C][switch.gpio:037]:     CH3 IA
[19:13:15][C][switch.gpio:068]: GPIO Switch 'CH4 IA'
[19:13:15][C][switch.gpio:091]:   Restore Mode: always OFF
[19:13:15][C][switch.gpio:031]:   Pin: 6 via SN74HC595
[19:13:15][C][switch.gpio:033]:   Interlocks:
[19:13:15][C][switch.gpio:037]:     CH4 IB
[19:13:15][C][switch.gpio:068]: GPIO Switch 'CH4 IB'
[19:13:15][C][switch.gpio:091]:   Restore Mode: always OFF
[19:13:15][C][switch.gpio:031]:   Pin: 7 via SN74HC595
[19:13:15][C][switch.gpio:033]:   Interlocks:
[19:13:15][C][switch.gpio:037]:     CH4 IA
[19:13:15][C][switch.gpio:068]: GPIO Switch 'CH5 IA'
[19:13:15][C][switch.gpio:091]:   Restore Mode: always OFF
[19:13:15][C][switch.gpio:031]:   Pin: 8 via SN74HC595
[19:13:15][C][switch.gpio:033]:   Interlocks:
[19:13:15][C][switch.gpio:037]:     CH5 IB
[19:13:15][C][switch.gpio:068]: GPIO Switch 'CH5 IB'
[19:13:15][C][switch.gpio:091]:   Restore Mode: always OFF
[19:13:15][C][switch.gpio:031]:   Pin: 9 via SN74HC595
[19:13:15][C][switch.gpio:033]:   Interlocks:
[19:13:15][C][switch.gpio:037]:     CH5 IA
[19:13:15][C][switch.gpio:068]: GPIO Switch 'CH6 IA'
[19:13:15][C][switch.gpio:091]:   Restore Mode: always OFF
[19:13:15][C][switch.gpio:031]:   Pin: 10 via SN74HC595
[19:13:15][C][switch.gpio:033]:   Interlocks:
[19:13:15][C][switch.gpio:037]:     CH6 IB
[19:13:15][C][switch.gpio:068]: GPIO Switch 'CH6 IB'
[19:13:15][C][switch.gpio:091]:   Restore Mode: always OFF
[19:13:15][C][switch.gpio:031]:   Pin: 11 via SN74HC595
[19:13:15][C][switch.gpio:033]:   Interlocks:
[19:13:15][C][switch.gpio:037]:     CH6 IA
[19:13:15][C][template.number:050]: Template Number 'bemf_trigger_1'
[19:13:15][C][template.number:051]:   Optimistic: YES
[19:13:15][C][template.number:052]:   Update Interval: 60.0s
[19:13:15][C][template.number:050]: Template Number 'bemf_trigger_2'
[19:13:15][C][template.number:051]:   Optimistic: YES
[19:13:15][C][template.number:052]:   Update Interval: 60.0s
[19:13:15][C][template.number:050]: Template Number 'bemf_trigger_3'
[19:13:15][C][template.number:051]:   Optimistic: YES
[19:13:15][C][template.number:052]:   Update Interval: 60.0s
[19:13:15][C][template.number:050]: Template Number 'bemf_trigger_4'
[19:13:15][C][template.number:051]:   Optimistic: YES
[19:13:15][C][template.number:052]:   Update Interval: 60.0s
[19:13:15][C][template.number:050]: Template Number 'bemf_trigger_5'
[19:13:15][C][template.number:051]:   Optimistic: YES
[19:13:15][C][template.number:052]:   Update Interval: 60.0s
[19:13:15][C][template.number:050]: Template Number 'bemf_trigger_6'
[19:13:15][C][template.number:051]:   Optimistic: YES
[19:13:15][C][template.number:052]:   Update Interval: 60.0s
[19:13:15][C][template.number:050]: Template Number 'min movement change %'
[19:13:15][C][template.number:051]:   Optimistic: YES
[19:13:15][C][template.number:052]:   Update Interval: 60.0s
[19:13:15][C][template.number:050]: Template Number '301_Heizkreis-WC_supply-flow-offset'
[19:13:15][C][template.number:051]:   Optimistic: YES
[19:13:15][C][template.number:052]:   Update Interval: 60.0s
[19:13:15][C][template.number:050]: Template Number '301_Heizkreis-WC_return-flow-offset'
[19:13:15][C][template.number:051]:   Optimistic: YES
[19:13:15][C][template.number:052]:   Update Interval: 60.0s
[19:13:15][C][template.number:050]: Template Number '301_Heizkreis-Wohnen-1_supply-flow-offset'
[19:13:15][C][template.number:051]:   Optimistic: YES
[19:13:15][C][template.number:052]:   Update Interval: 60.0s
[19:13:15][C][template.number:050]: Template Number '301_Heizkreis-Wohnen-1_return-flow-offset'
[19:13:15][C][template.number:051]:   Optimistic: YES
[19:13:15][C][template.number:052]:   Update Interval: 60.0s
[19:13:15][C][template.number:050]: Template Number '301_Heizkreis-Wohnen-2_supply-flow-offset'
[19:13:15][C][template.number:051]:   Optimistic: YES
[19:13:15][C][template.number:052]:   Update Interval: 60.0s
[19:13:15][C][template.number:050]: Template Number '301_Heizkreis-Wohnen-2_return-flow-offset'
[19:13:15][C][template.number:051]:   Optimistic: YES
[19:13:15][C][template.number:052]:   Update Interval: 60.0s
[19:13:15][C][template.number:050]: Template Number '301_Heizkreis-Kueche_supply-flow-offset'
[19:13:15][C][template.number:051]:   Optimistic: YES
[19:13:15][C][template.number:052]:   Update Interval: 60.0s
[19:13:15][C][template.number:050]: Template Number '301_Heizkreis-Kueche_return-flow-offset'
[19:13:15][C][template.number:051]:   Optimistic: YES
[19:13:15][C][template.number:052]:   Update Interval: 60.0s
[19:13:15][C][template.number:050]: Template Number '301_Heizkreis-Flur-1_supply-flow-offset'
[19:13:15][C][template.number:051]:   Optimistic: YES
[19:13:15][C][template.number:052]:   Update Interval: 60.0s
[19:13:15][C][template.number:050]: Template Number '301_Heizkreis-Flur-1_return-flow-offset'
[19:13:15][C][template.number:051]:   Optimistic: YES
[19:13:15][C][template.number:052]:   Update Interval: 60.0s
[19:13:15][C][template.number:050]: Template Number '301_Heizkreis-Flur-2_supply-flow-offset'
[19:13:15][C][template.number:051]:   Optimistic: YES
[19:13:15][C][template.number:052]:   Update Interval: 60.0s
[19:13:15][C][template.number:050]: Template Number '301_Heizkreis-Flur-2_return-flow-offset'
[19:13:15][C][template.number:051]:   Optimistic: YES
[19:13:15][C][template.number:052]:   Update Interval: 60.0s
[19:13:15][C][template.sensor:022]: Template Sensor '301_Heizkreis-WC_spreading'
[19:13:15][C][template.sensor:022]:   State Class: ''
[19:13:15][C][template.sensor:022]:   Unit of Measurement: '°C'
[19:13:15][C][template.sensor:022]:   Accuracy Decimals: 2
[19:13:15][C][template.sensor:023]:   Update Interval: 10.0s
[19:13:15][C][template.sensor:022]: Template Sensor '301_Heizkreis-Wohnen-1_spreading'
[19:13:15][C][template.sensor:022]:   State Class: ''
[19:13:15][C][template.sensor:022]:   Unit of Measurement: '°C'
[19:13:15][C][template.sensor:022]:   Accuracy Decimals: 2
[19:13:15][C][template.sensor:023]:   Update Interval: 10.0s
[19:13:15][C][template.sensor:022]: Template Sensor '301_Heizkreis-Wohnen-2_spreading'
[19:13:15][C][template.sensor:022]:   State Class: ''
[19:13:15][C][template.sensor:022]:   Unit of Measurement: '°C'
[19:13:15][C][template.sensor:022]:   Accuracy Decimals: 2
[19:13:15][C][template.sensor:023]:   Update Interval: 10.0s
[19:13:15][C][template.sensor:022]: Template Sensor '301_Heizkreis-Kueche_spreading'
[19:13:15][C][template.sensor:022]:   State Class: ''
[19:13:15][C][template.sensor:022]:   Unit of Measurement: '°C'
[19:13:15][C][template.sensor:022]:   Accuracy Decimals: 2
[19:13:15][C][template.sensor:023]:   Update Interval: 10.0s
[19:13:15][C][template.sensor:022]: Template Sensor '301_Heizkreis-Flur-1_spreading'
[19:13:15][C][template.sensor:022]:   State Class: ''
[19:13:15][C][template.sensor:022]:   Unit of Measurement: '°C'
[19:13:15][C][template.sensor:022]:   Accuracy Decimals: 2
[19:13:15][C][template.sensor:023]:   Update Interval: 10.0s
[19:13:15][C][template.sensor:022]: Template Sensor '301_Heizkreis-Flur-2_spreading'
[19:13:15][C][template.sensor:022]:   State Class: ''
[19:13:15][C][template.sensor:022]:   Unit of Measurement: '°C'
[19:13:15][C][template.sensor:022]:   Accuracy Decimals: 2
[19:13:15][C][template.sensor:023]:   Update Interval: 10.0s
[19:13:15][C][template.sensor:022]: Template Sensor 'Spreading-Target'
[19:13:15][C][template.sensor:022]:   State Class: ''
[19:13:15][C][template.sensor:022]:   Unit of Measurement: '°C'
[19:13:15][C][template.sensor:022]:   Accuracy Decimals: 2
[19:13:15][C][template.sensor:023]:   Update Interval: 15.0s
[19:13:15][C][template.sensor:022]: Template Sensor '301_Heizkreis-WC_return-flow-target'
[19:13:15][C][template.sensor:022]:   State Class: ''
[19:13:15][C][template.sensor:022]:   Unit of Measurement: '°C'
[19:13:15][C][template.sensor:022]:   Accuracy Decimals: 2
[19:13:15][C][template.sensor:023]:   Update Interval: 15.0s
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

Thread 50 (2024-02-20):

Need help - Order Error jlcpcb.com

grericht, 2024-02-20:
Get this Error ordering by jlcpcb.com

The below parts won't be assembled due to data missing.
WROOM-LEFT1,WROOM-RIGHT,WROOM-LEFT,HLK-PM03,P1,P2,P3,P4,H4,H5,OPAMP-H1,U1 designators don't exist in the BOM file.

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

nliaudat, 2024-02-20:
For P5 to P12 +  Screw-230V, select part #C8465
H1, H3 are holes, the is no part

nliaudat, 2024-02-20:
[BOM_esp32-8ch-dc-motor-shield_AC_2024-02-20.csv](https://github.com/nliaudat/esp32_8ch_motor_shield/files/14349458/BOM_esp32-8ch-dc-motor-shield_AC_2024-02-20.csv)
New BOM file

nliaudat, 2024-02-20:
https://github.com/nliaudat/esp32_8ch_motor_shield/releases/tag/v58_rev_1.52

grericht, 2024-02-23:
new bom file still not working. but using part #C8465 helps!

Closed 2024-02-20.

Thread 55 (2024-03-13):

[BUG] - short circuit at BMEF in Bord: v57 rev 1.48

DerMo92, 2024-03-13:
<!-- Thanks for reporting a bug for this project. READ THIS FIRST:

- Provide as many details as possible. Simply saying "X gives bug" or "X gives error" is not enough!
- Paste logs, configuration sample and code into the backticks (```).
- Read through the template carefully and fill out all missing details.
- Please also search for similar issues in this issue tracker first and read through the ESPHome FAQ.

DO NOT DELETE ANY TEXT from this template! Otherwise the issue may be closed without a comment.
-->

**Operating environment/Installation (Hass.io/Docker/pip/etc.):**
<!--
Please provide details about your environment below this line. -->

**ESP (ESP32/ESP8266, Board/Sonoff):**
<!--
Please provide details about which ESP you're using below.
-->

**ESPHome version (latest production, beta, dev branch)**
<!--
ESPHome version like v1.14 or 1.15-dev
-->

**Affected component:**
<!--
Please add the link to the documentation at https://esphome.io/index.html of the component in question.
-->

**Description of problem:**

Bord: v57 rev 1.48
At latest version of this Board with RJ10. I wanted to use this version since I'm using the original Motors with RJ10 Plug.
while using it the BMEF ( Mesures of the Channels to see if end stops
are reached) I always got 0,008V. That is basically short circuit. After a long investigation with a friend we found out, that all four channels have a short circuit to ground at the pin holes though the board. Compared to the latest version they are not isolated at the bottom layer to the Ground Polygone. (check images below)
I suggest a warning in the Documentation for now and at best a correction in the Gerberfile. For me it was too late - we repaired it manually - for anyone who has the same issue check below.

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

**Problem-relevant YAML-configuration entries:**
```yaml
PASTE YAML FILE HERE

```

**Logs (if applicable):**
<!--
Please copy the debug log here. If possible, also connect to the ESP over USB and copy those logs into the backticks.
-->
```
PASTE DEBUG LOG HERE

```

**Additional information and things you've tried:**

<!-- LEAVE THIS LINE AS-IS AND DON'T DELETE IT, OTHERWISE THE ISSUE WILL BE CLOSED AUTOMATICALLY. -->

nliaudat, 2024-03-13:
Many thanks for showing that issue.
I've corrected the release https://github.com/nliaudat/esp32_8ch_motor_shield/releases/tag/v57

It's too late, but I recommend you to use only the latest versions, even if the connectors no longer use RJ11.
Just cut your cables and follow https://github.com/nliaudat/esp32_8ch_motor_shield/blob/main/VDMOT_wiring.md.

Thanks again for this bug report.

Closed 2024-03-13.

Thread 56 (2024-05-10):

Need help

rzerres, 2024-05-10:
Try to improve the ordering via JLPCB

Dear Nicolas,

This is great work.

Since I'm rebuilding an apartment, I'd like to use this PCB to control my newly installed underfloor heating.
I was amazed and completely satisfied when i got hold of this repository. I do have 4 circles that should be managed via individual porportional actors.
The given documentation my be a bit rough for newcomers like me. So i took the time to prepare a PR that introduces an "HOWTO_get_going.md".
I will submit it once i finished some last shaping.

May you can enlight me to solve following questions:

1. Is the given box design (box-V57rev-1.48) compatible with the upstream controller (PCB_PCB v58 rev 1.51_2023-10-02.pdf)?
2. The controller is fully configurable via home-assistant?
3. I'd like to order via JLPCB
   Since it will be the first time usage for me, I'd like to describe the process to ease the process.
   - register an accout
   - which "part list" has to be uploaded in the JLPCB Gui to include
     * ESP32-WROOM-32D or ESP32-WROOM-32U
	 * The Controller is able trigger the motors of open proportional
	   (like percentage, triggered by temprature sensor?
 4. Can you advise a good input AC Power (presumable a 5V for HKL-5MX)?

nliaudat, 2024-05-10:
Hi,

I'll try to respond quickly :

1) no, the box is for RJ11 version. It may fit, but I suggest you to investigate the openscad version : [PCB_box_generator_v1-1.scad](https://github.com/nliaudat/esp32_8ch_motor_shield/blob/main/box/general/PCB_box_generator_v1-1.scad)
2) Yes, the controller is fully compatible with hassio as it runs esphome.
3)

- a :

ESP32-WROOM-32D or U version (with external antenna) has to be bought elsewhere than JLCPCB cause the price in JLCPCB is huge. You may find your needs in aliexpress or others.

- b:

The controller works in proportionnal mode. The temperature difference between target temp and real temp triggers a movement every 15 minutes. There is a version of firmware with a PID controll.  You can control it with hassio or standalone. You'll find futher informations on https://github.com/nliaudat/floor-heating-controller/wiki/

4) For the Ac power, most proportionnal valves use 3.3V as esp32. I'll recommend to use HKL-5M03 or HKL-PM03
Actually, if you buy the HKL-XX component at JLCPC, the weight is misscalculated and the freight cost is huge. I'll recommend you to buy it separatly and solder yourself.

Have a look at https://github.com/Lenti84/VdMot_Controller before buying one of mine. You may have the choice of 2 solutions.

Regards

rzerres, 2024-05-10:
Thanks. This advise is quite helpful.

One more question:
Vendor documentation states ESP32-WROOM-32D and ESP32-WROOM-32U deprecated. If I did read correctly, ESP32WROOM32E and ESP32WROOM32UE are their successors. Will the firmware will work without adaption?

nliaudat, 2024-05-11:
> Thanks. This advise is quite helpful.
>
> One more question: Vendor documentation states ESP32-WROOM-32D and ESP32-WROOM-32U deprecated. If I did read correctly, ESP32WROOM32E and ESP32WROOM32UE are their successors. Will the firmware will work without adaption?

All boards supported by platformio and esp-idf frameworks should compile esphome.

https://docs.platformio.org/en/latest/platforms/espressif32.html#boards

rzerres, 2024-05-13:
How about this one?

https://www.reichelt.de/entwicklungsboard-esp32-wroom-32e-esp32devkitc32e-p341303.html?&nbc=1

nliaudat, 2024-05-14:
Hi,

I'm surprised at the price of the card at Reichelt, which is over €10...
I would still advise you to stick with a well-known card (ESP32-WROOM-32D 38p) available on Aliexpress for example. You'll find one for 3€.

With the Gerber files, you can order a PCB from anywhere.
I don't give the EasyEda sources any more, because some people made modifications, ordered and then complained that it didn't work.

What's more, no one has proposed any public changes to the PCB board in 5 years.

I also no longer support older versions because some components are no longer available.
You must use the latest version:  https://github.com/nliaudat/esp32_8ch_motor_shield/releases/tag/v58_rev_1.52
Unzip it and you'll find the files you need to ordrer.

Regards

rzerres, 2024-05-14:
Thanks. I will go with that.

And i completely understand Not offering the gerbers any more. Quite offending If someone changes the layout then complains and requires your Support. Not in line with Open source  Code of conduct.

nliaudat, 2024-05-14:
> Thanks. I will go with that.
>
> And i completely understand Not offering the gerbers any more. Quite offending If someone changes the layout then complains and requires your Support. Not in line with Open source Code of conduct.

I offer the gerbers ! The schematics and you need. But not the EasyEda source :
 https://github.com/nliaudat/esp32_8ch_motor_shield/releases/tag/v58_rev_1.52

Closed 2024-05-22.

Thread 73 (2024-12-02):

5V power supply of ESP32

THorst92, 2024-12-02:
Hi, I have one question:
As far as I understand the board, the ESP32 is powered by defaut with 3.3V.
Do I have to remove the diode connection between the ESP32 and 5V then? Or is this part not included in the BOM?
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

nliaudat, 2024-12-02:
Hi,
The esp32 board is powered with 5V ( 5-12V) as esp32 has is own voltage regulator.
The diode is here to not discarge esp32 dedicaded capacitors.
Do not remove the diode.

nliaudat, 2024-12-02:
https://github.com/nliaudat/esp32_8ch_motor_shield/wiki/Project-rules

Closed 2024-12-02.

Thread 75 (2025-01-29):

Need Help - CPL and BOM files missing in pcb V61

Keff789, 2025-01-29:
<!-- READ THIS FIRST:

################
READ rules (https://github.com/nliaudat/esp32_8ch_motor_shield/wiki/Project-rules) before posting !
################

 - This is for supporters "need help" only, for issues please go to the issues repository.
 - Please be as descriptive as possible, especially use-cases that can otherwise not be solved boost the problem's priority.

 DO NOT DELETE ANY TEXT from this template! Otherwise the issue may be closed without a comment.

Please accept the delay could be greater to respond.

Give as many details as you can

-->

Hello,

is it possible that the CPL and BOM files are missing in the gerber files for the V61 Version, or where can i find them?

Thanks a lot!

nliaudat, 2025-02-13:
Sorry for the late response, I've missed your issue.
I've added the missing files .

Regards

Closed 2025-02-13.

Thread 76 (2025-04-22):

Need help - Error when uploading BOM & CPL to JLCPCB

pedrosalgueiro, 2025-04-22:
Hi,

First of all, thank you for this awsome project!

I am considering to order some v61 PCBs from JLCPCB, and I am getting the following error when uploading BOM & CPL files:

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

Is there a problem with BOM or CPL files? Or is it something that I am doing wrong?

Also, if I continue and ignore the error, some parts, such as the 5-12V input seems to be missing:

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

Appreciate any help with this.

Best regards

nliaudat, 2025-04-23:
Sry, no time actually.

Have you tried to generate a new BOM in [https://oshwlab.com/nliaudat/floor_heatin_controller_v61](https://pro.easyeda.com/editor#id=15bc77acaa4147fca2a36e92e8cc8681) ?

Closed 2025-04-24.

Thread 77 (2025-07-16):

Need help with xlsx/csv

konkro, 2025-07-16:
Hey unfortunatelly i have no clue about Gerber and bom but there seems to be an issue with some parts while uploding and processing the files at JLCPCB. some parts are missing some info: "supermini-1,WROOM-LEFT2,5-12V-input,H1,WROOM-LEFT1,WROOM-RIGHT1"

I'd love to buy the boards from someone else, the process looks to be a bit to much to me :D

nliaudat, 2025-07-17:
that parts are not real parts.
That's footprints.
If you want more help refer to https://github.com/nliaudat/esp32_8ch_motor_shield/wiki/Project-rules
Regards

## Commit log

2021-10-30 v85
    # change log v85 :
    #Rollback function tested (bug)
    # add esp32: routine
    # flash_write_interval: 60min
    # Substitution for names
    # replace check_interval loop in climate.thermostat by interval (or time)
    # Number for parameters like BEMF triggers
    # One BEMF trigger param per channel
    # add idle global variable for thermostat
    # Re test pid climate with that parameters for low temperature heating : kp: 30 ki: 0.005 kd: -24000
    # Test current_base_cover : done but do not work as expected : endstop triggered as FLT_MAX parameter is reach but FLT_MAX is position. I do not understand.
2021-11-19 add power
2021-11-19 5V power
2022-09-14 Create pcb
2023-03-18 restore sources
    [BOM_esp32-8ch-dc-motor-shield_AC_2023-03-18.csv, PCB v58 rev 1.50_2023-03-18.pcbdoc, PickAndPlace_PCB v58 rev 1.50_2023-03-18.csv]
2023-05-08 fix directories
    [PCB_box_generator_body.stl, PCB_box_generator_cover.stl, PCB_box_generator_v1-1.scad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]
2023-05-08 move files
    [PCB_box_generator_body.stl, PCB_box_generator_cover.stl, PCB_box_generator_v1-1.scad]
2024-05-10 Introduce HOWTO_get_going.md
    Updating the documentation that describes the steps to create a custom
    PCB including ordering via JCPCB and printout an enclosure
2024-05-10 Add Images to HmIP-VDMOT actuators
2024-05-10 Remove wrong or misleading references
    - vendor reference to HmIP-FALMOT-12
    - Correct referencing as an ESP32 board
